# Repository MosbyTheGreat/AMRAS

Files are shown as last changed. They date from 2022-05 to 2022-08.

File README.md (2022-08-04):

# AMRAS
Anti-Mitbewohner-Raketen-Abwehr-System (engl. Anti Roommate Rocket Defence System)

An automated turret, which uses a combination of a Raspberry Pi, a camera, some servos, transformers and rubbing alcohol
to propel rubber rockets into anyone's face who dares to enter its vicinity.

The build manual can be found [here](./Manual/AMRAS%20Build%20Manual.pdf).

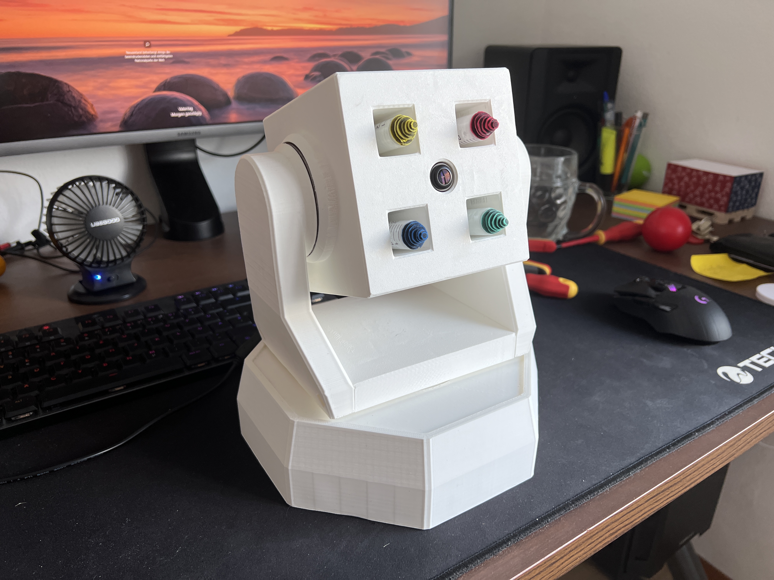
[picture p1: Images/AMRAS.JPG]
AMRAS


## Parts List

 - Raspberry Pi 3B (Good Luck finding one, but should also work with newer versions)  
 - Power Supply: https://www.amazon.de/gp/product/B07DG16TKS/ref=ppx_yo_dt_b_search_asin_title?ie=UTF8&psc=1  
 - Camera: https://de.aliexpress.com/item/32668508991.html  
 - Servo Controller: https://de.aliexpress.com/item/4000468996665.html  
 - 4x Transformer/Spark Generator: https://de.aliexpress.com/item/32872820437.html  
 - 2x Servo: https://de.aliexpress.com/item/32970493831.html  
 - 4-Band Relay: https://de.aliexpress.com/item/4001363470793.html  
 - Some Cables: https://de.aliexpress.com/item/33060775595.html  
 - 3x Ball Bearing: https://www.amazon.de/gp/product/B076ZL83YN/ref=ppx_yo_dt_b_asin_title_o03_s00?ie=UTF8&psc=1  
 - 4x Mini Magnets for keeping the Lid shut: https://www.magnet-shop.net/neodym/quadermagnete/quadermagnet-10.0-x-5.0-x-3.0-mm-n40-nickel-haelt-1.4-kg  
 - Syringes to craft Rockets out of: https://www.amazon.de/gp/product/B07MC7L4PG/ref=ppx_yo_dt_b_search_asin_image?ie=UTF8&psc=1  
 - Bunch of Screws (I used Wood screws to screw into the PLA):  
Raspi: 4x 2,0x10mm  
Kamera: 4x 2,0x10mm  
Main Body Fillings: 24x 2,9x13mm  
Arms: 4x 2,9x13mm  
Servo Shield: 4x 2,0x10mm  
Relais: 1x 2,0x10mm  

## Feature Ideas

 - Stereo camera to calculate distances and trajectory of projectiles
 - Different kinds of projectiles
 - Better servos to allow for 360° coverage
 - Live video feed to smartphone with manual control

## TODO
 - PID tuning
 - Script for camera calibration

## Credits

Initially inspired by this video:  
https://youtu.be/U4ndTDGhc1U

Credit to Adrian Rosebrock, PhD, from pyimagesearch.com for this wonderful tutorial, which my face tracking code is based on:  
https://www.pyimagesearch.com/2019/04/01/pan-tilt-face-tracking-with-a-raspberry-pi-and-opencv/

Also thanks to my roommate [Florian Geißegger BSc](mailto:florian.geissegger@gmx.com) for helping me with the soldering and for some general technical input.

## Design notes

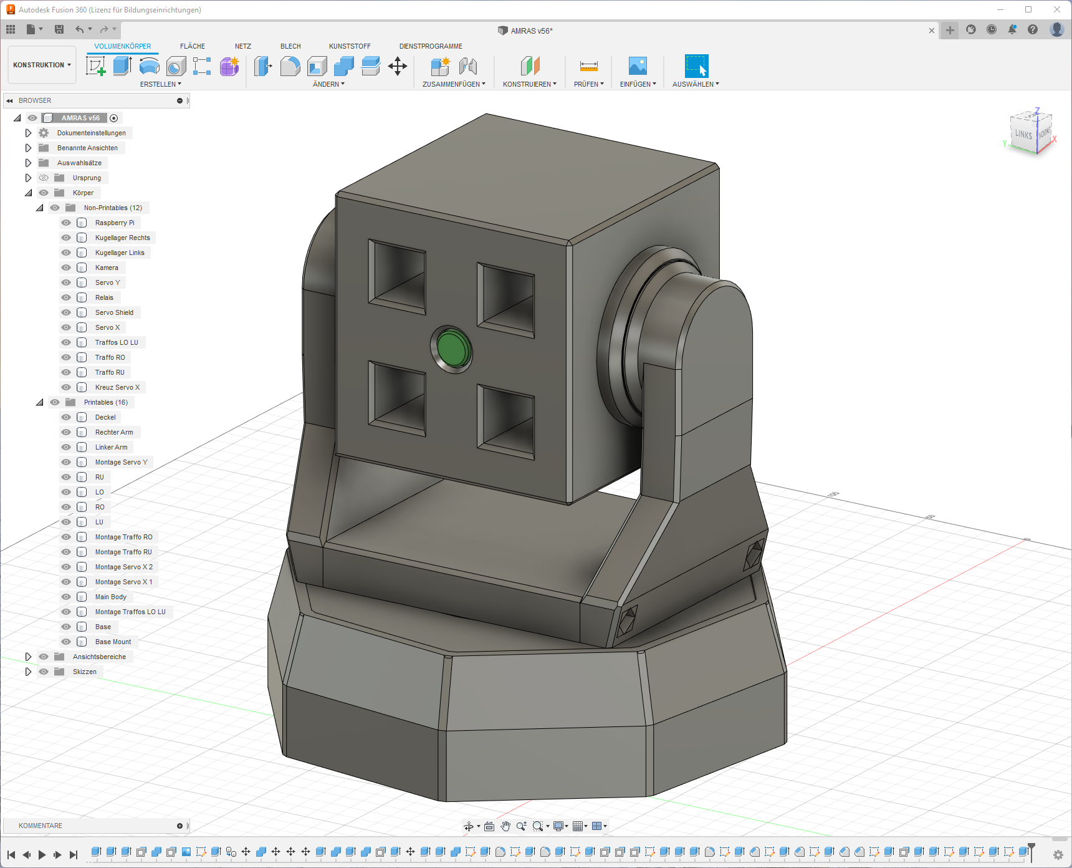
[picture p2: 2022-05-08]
Images/Fusion.png

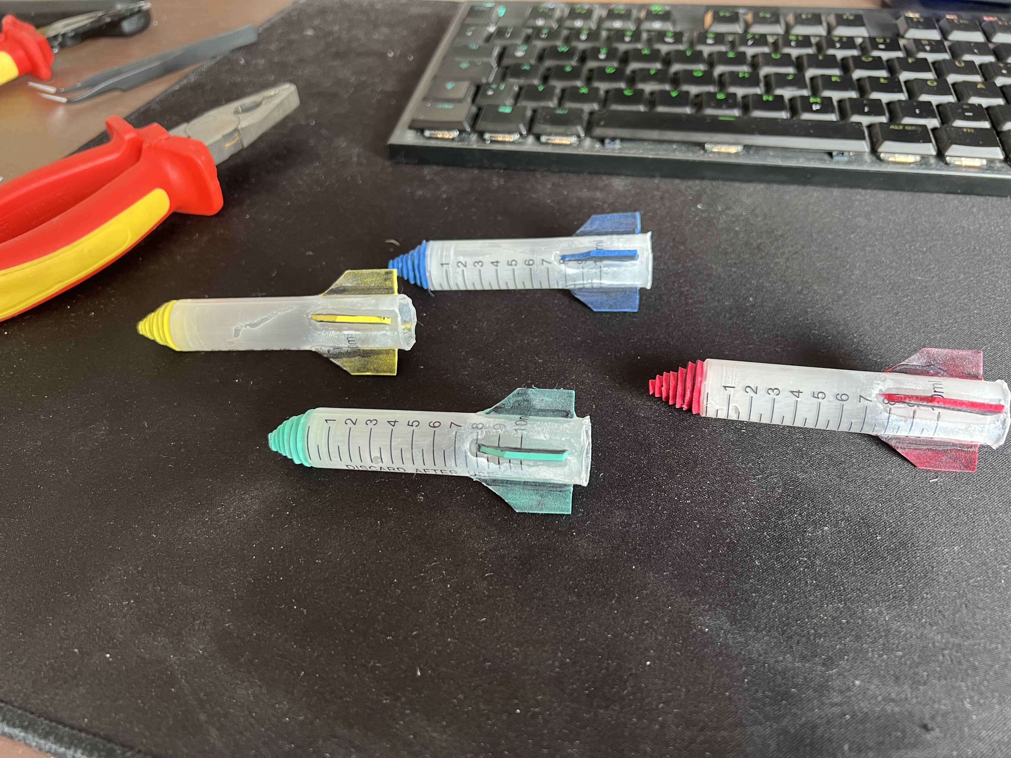
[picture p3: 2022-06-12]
Images/Rockets.JPG

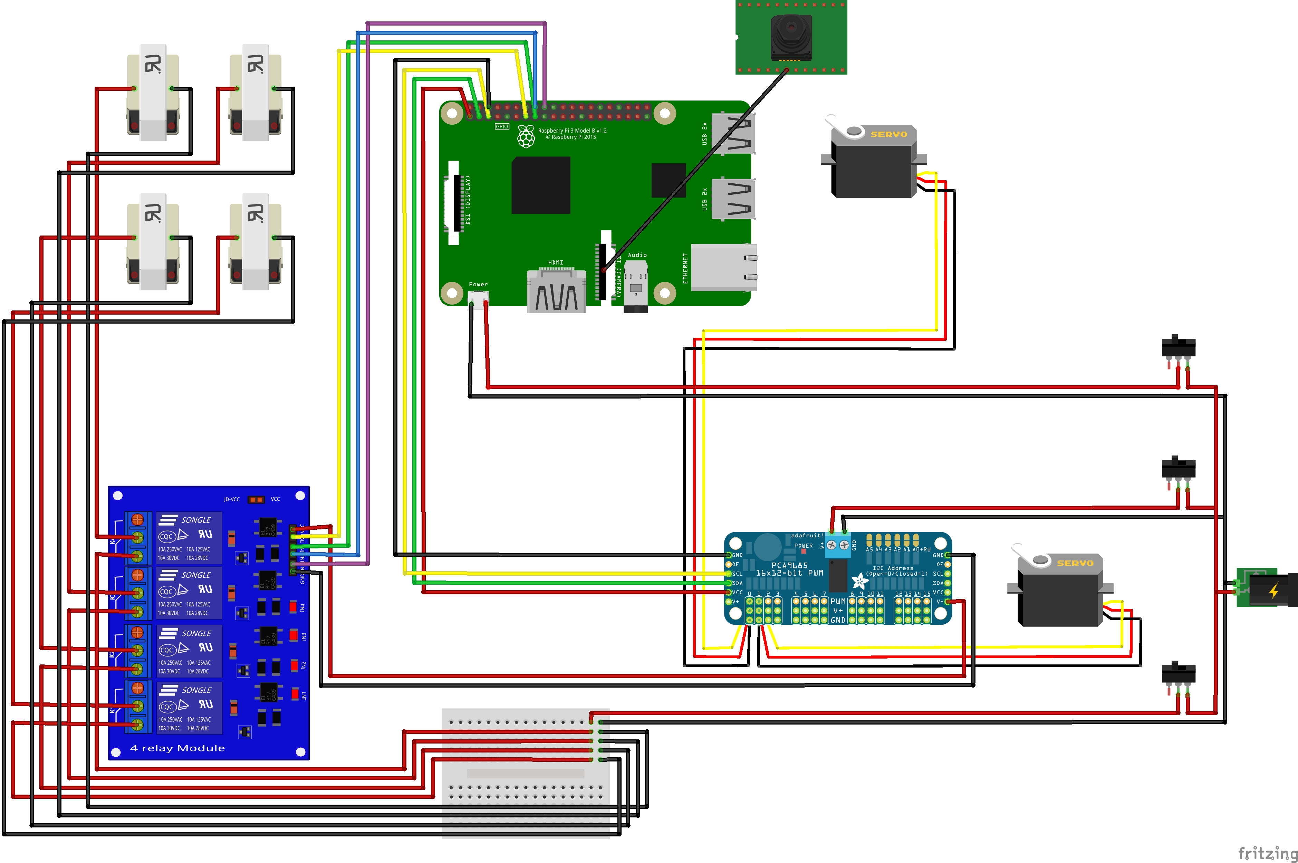
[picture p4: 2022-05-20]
Circuit Diagram/circuit_diagram.jpg

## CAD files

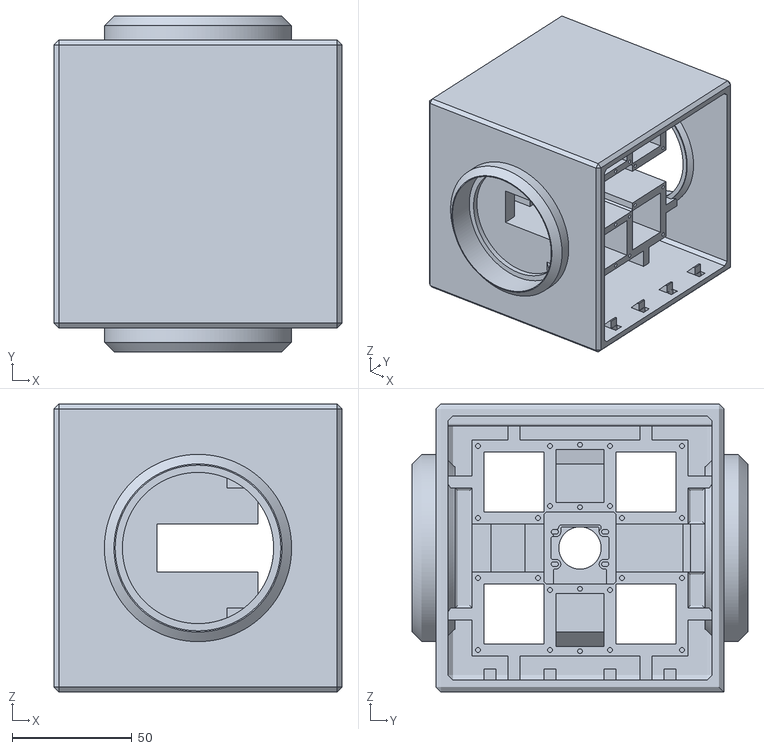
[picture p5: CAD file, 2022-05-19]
3D Files/Main Body.stl
120.0 x 140.0 x 120.0

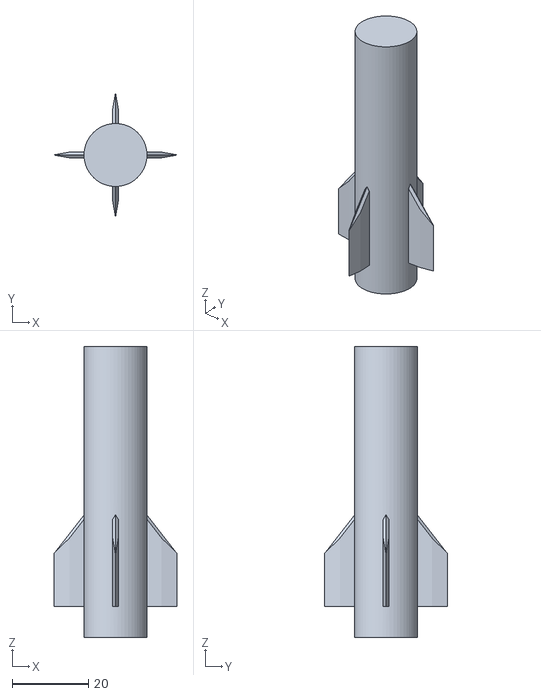
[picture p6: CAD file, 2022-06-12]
3D Files/Missile Fuelcell Flat Tip.stl
32.1 x 32.1 x 76.2

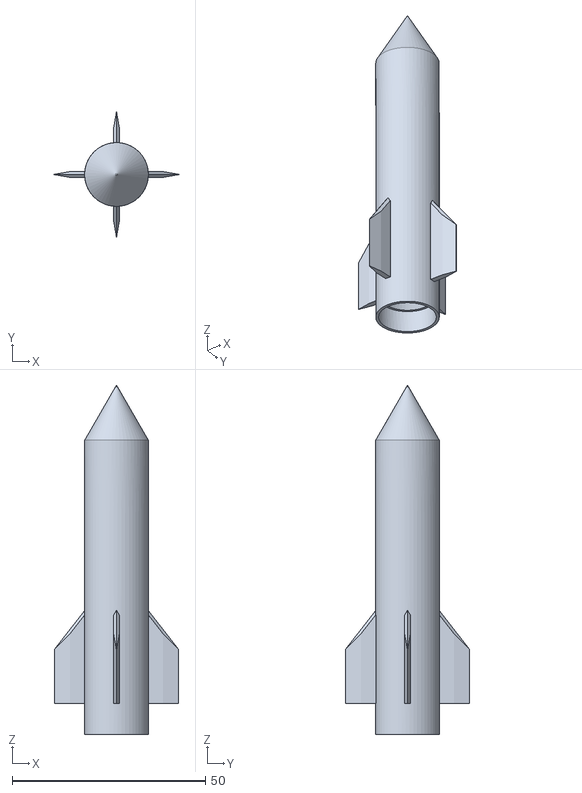
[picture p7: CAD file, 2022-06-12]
3D Files/Missile Fuelcell Spikyboi.stl
32.1 x 32.1 x 90.3

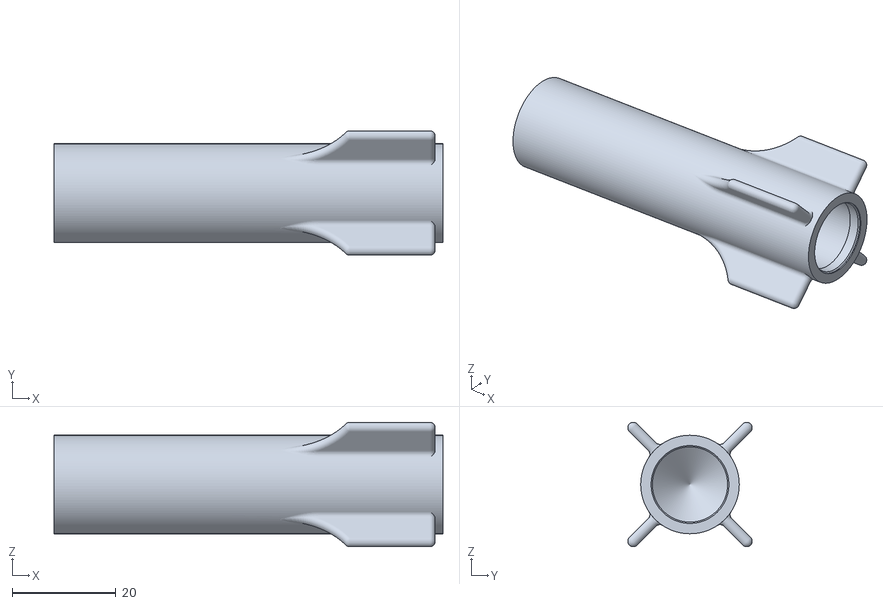
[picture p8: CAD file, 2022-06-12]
3D Files/Missile.stl
75.0 x 24.0 x 24.0

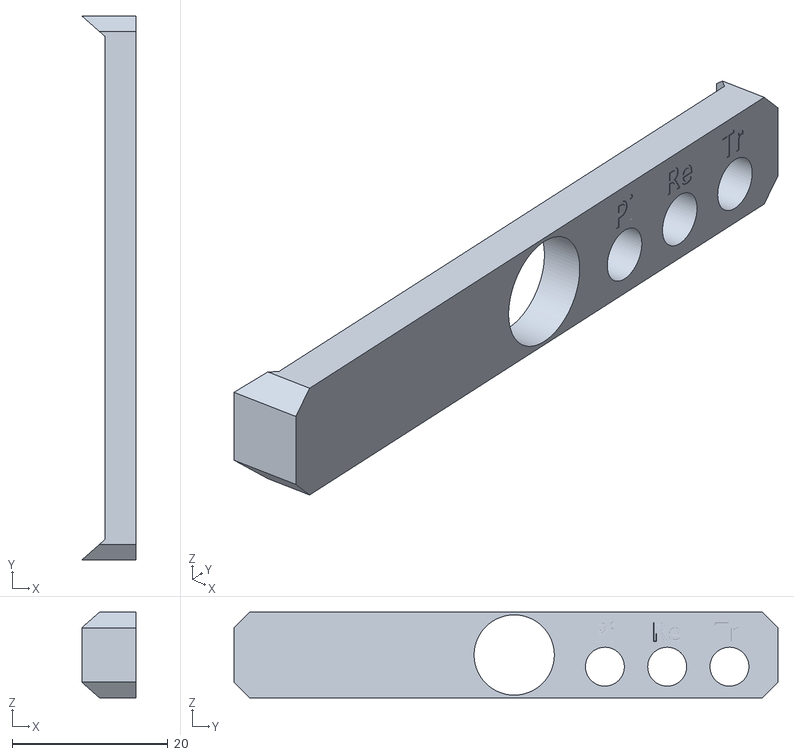
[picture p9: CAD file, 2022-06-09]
3D Files/Power Panel.stl
7.00 x 69.9 x 11.0

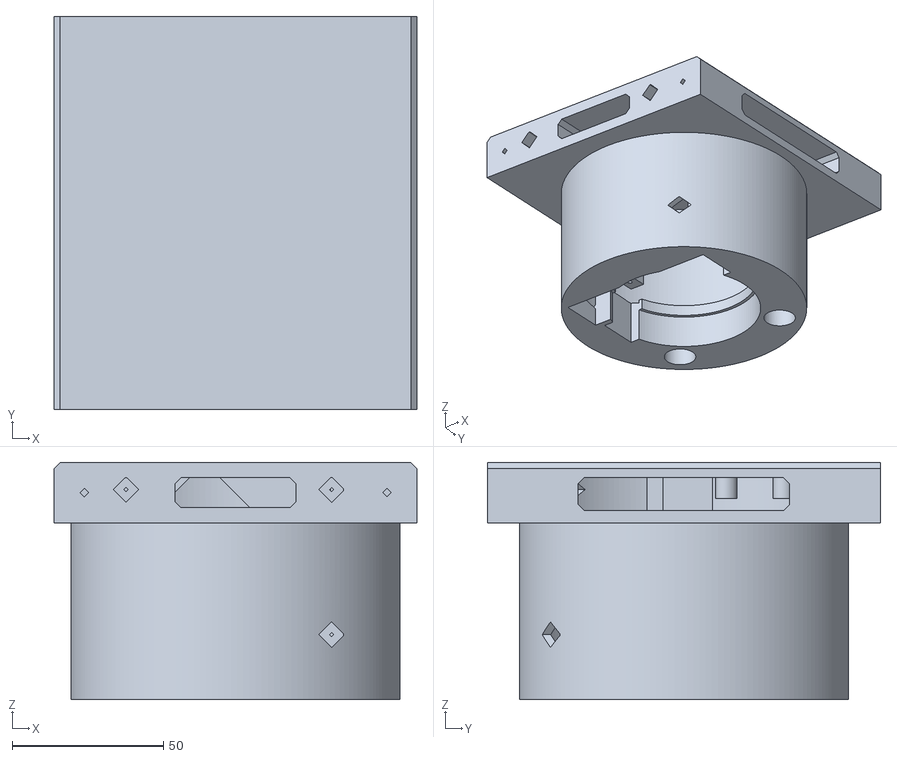
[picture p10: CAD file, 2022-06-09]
3D Files/Base Mount.stl
120.0 x 130.0 x 78.5

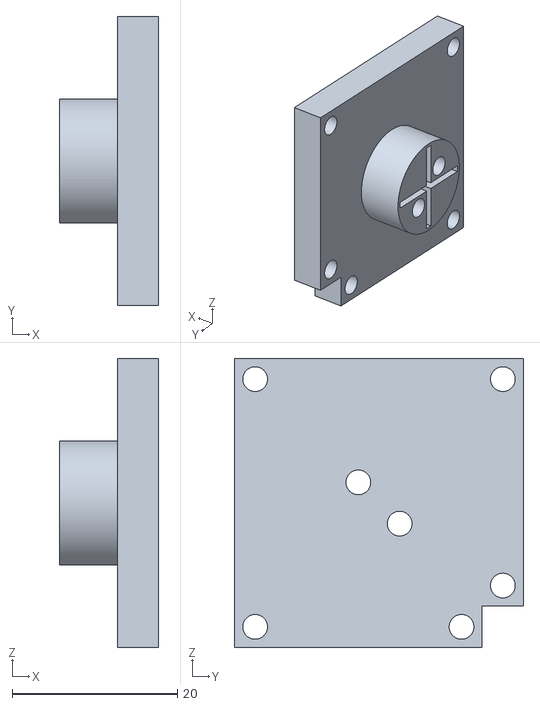
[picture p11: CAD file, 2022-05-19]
3D Files/LO.stl
12.0 x 35.0 x 35.0

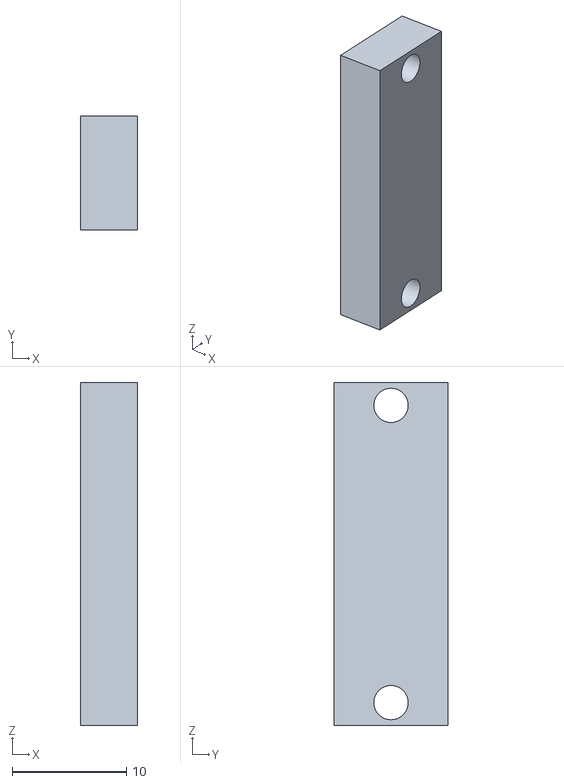
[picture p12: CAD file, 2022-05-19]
3D Files/Mount Traffo RU.stl
5.00 x 10.0 x 30.0

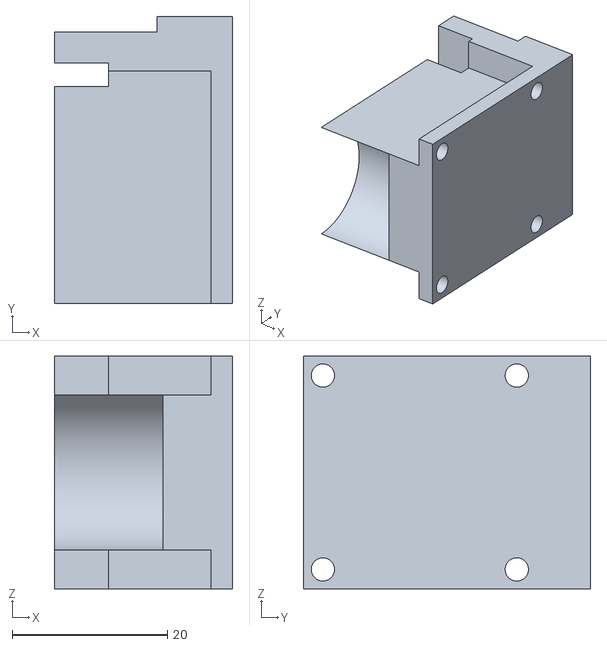
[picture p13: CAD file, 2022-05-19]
3D Files/Mount Servo Y.stl
23.0 x 37.0 x 30.0

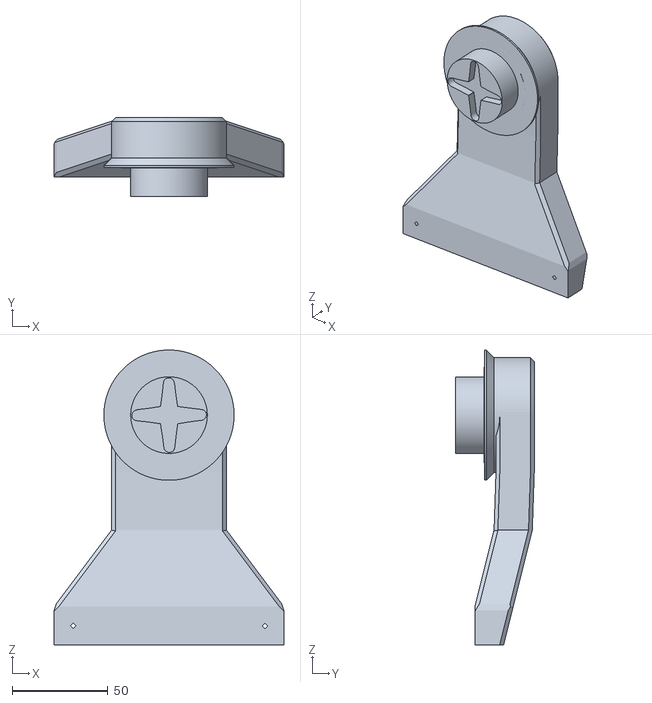
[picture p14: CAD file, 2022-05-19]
3D Files/Right Arm.stl
120.0 x 41.0 x 154.0

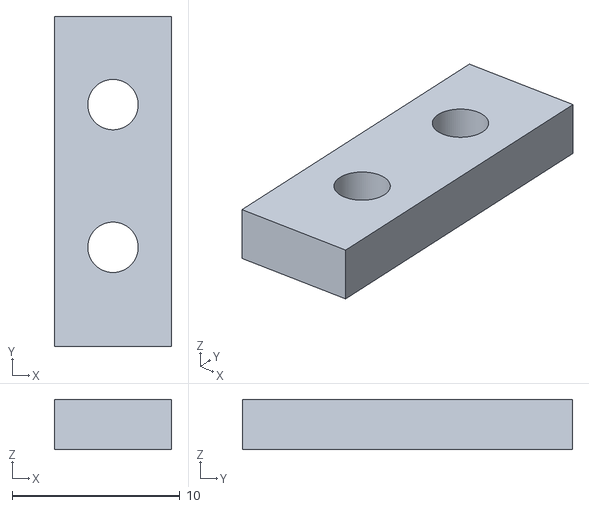
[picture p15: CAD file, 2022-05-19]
3D Files/Mount Servo X 2.stl
7.00 x 19.7 x 3.00

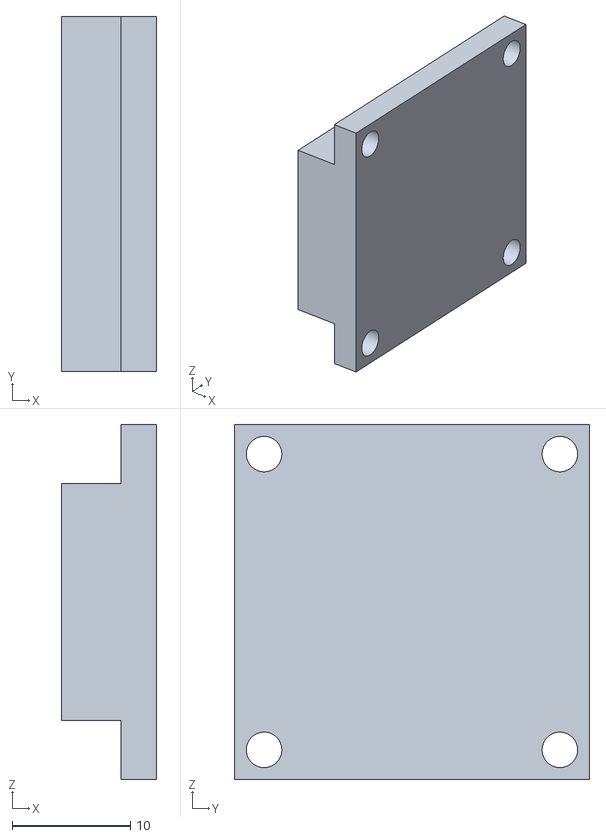
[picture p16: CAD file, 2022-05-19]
3D Files/Mount Traffos LO LU.stl
8.00 x 30.0 x 30.0

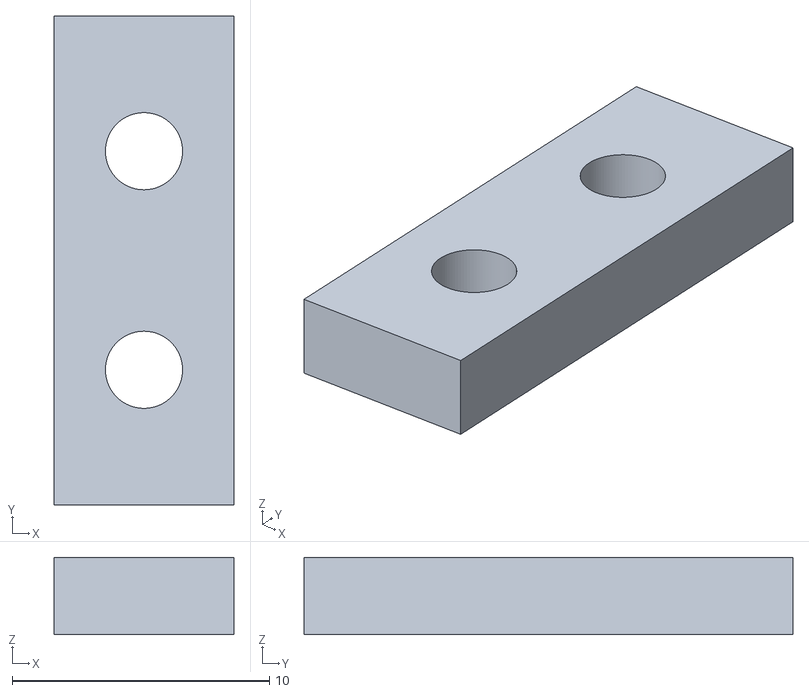
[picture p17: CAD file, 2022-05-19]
3D Files/Mount Servo X 1.stl
7.00 x 19.0 x 3.00

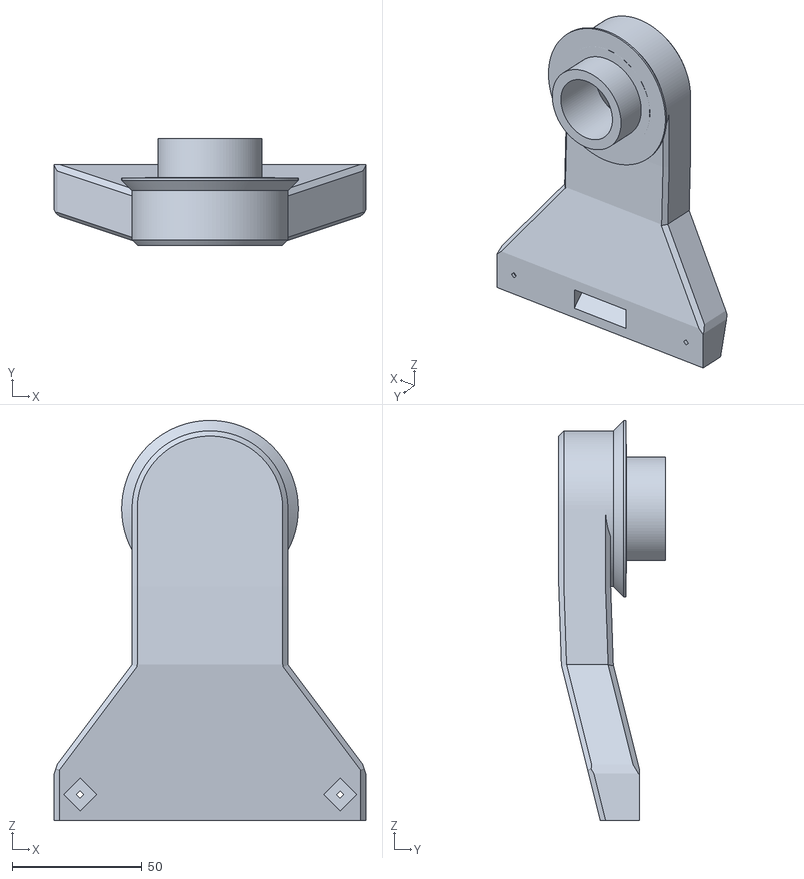
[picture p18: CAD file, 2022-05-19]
3D Files/Left Arm.stl
120.0 x 41.0 x 154.0

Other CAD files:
3D Files/RO.stl
3D Files/Mount Traffo RO.stl
3D Files/RU.stl
3D Files/Base.stl
3D Files/LU.stl
3D Files/Lid.stl

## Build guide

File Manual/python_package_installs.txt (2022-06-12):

Package installs:
sudo pip3 install opencv-python
sudo pip3 install smbus
sudo pip3 install imutils
sudo pip3 install "camera[array]"
sudo pip3 install adafruit_servokit
sudo pip3 install adafruit_motor
sudo pip3 install numpy
sudo pip3 install matplotlib

use 'sudo raspi-config' to go to raspberry pi configurantion and enable i2c & camera

Command for Starting program:
python3 init_amras.py -c frontalface.xml

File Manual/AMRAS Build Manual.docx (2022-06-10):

# AMRAS Build Manual

Screencap from the 3D Model in Fusion

# Introduction

AMRAS is the abbreviation for the German long form “Anti-Mitbewohner-Raketen-Abwehr-System” which translates to Anti-Roommate-Rocket-Defence-System.

It uses a combination of a Raspberry Pi, a camera, some servos, trafos and methylated spirits to propel rubber rockets into anyone’s face who dares to enter its vicinity

This guide will show you how to build and start it, have fun!

I got inspired when reddit flushed this video (https://youtu.be/U4ndTDGhc1U) onto my frontpage and I thought “that’s kinda cool, but I have a 3D printer and a Raspberry Pi, I could do that better”.

My code is based on Adrian Rosebrock’s tutorial (https://www.pyimagesearch.com/2019/04/01/pan-tilt-face-tracking-with-a-raspberry-pi-and-opencv/) who used a similar setup to track faces. While he used a PID controller for moving the servos, I had to fall back to a simpler movement, but this will hopefully soon be fixed.

# Parts List

These are not affiliate links, just the parts I used. It should also work with slightly different hardware, but then you would need to adapt the 3D models for mounting holes

- A Raspberry Pi 3B (a newer version should also work, but this is what I have tested with
- A 5V Power supply and some way of distributing power
- Camera (https://de.aliexpress.com/item/32668508991.html)
- Servo Controller (https://de.aliexpress.com/item/4000468996665.html)
- 4x Transformer/Spark generator (https://de.aliexpress.com/item/32872820437.html)
- 2x Servo (https://de.aliexpress.com/item/32970493831.html)
- 4-Band Relais (https://de.aliexpress.com/item/4001363470793.html)
- Some Cables (https://de.aliexpress.com/item/33060775595.html)
- 3x Ball Bearing (https://www.amazon.de/gp/product/B076ZL83YN/ref=ppx_yo_dt_b_asin_title_o03_s00?ie=UTF8&psc=1)
- 4x Mini Magnets (https://www.magnet-shop.net/neodym/quadermagnete/quadermagnet-10.0-x-5.0-x-3.0-mm-n40-nickel-haelt-1.4-kg) for keeping the lid shut
- Syringes (https://www.amazon.de/gp/product/B07MC7L4PG/ref=ppx_yo_dt_b_search_asin_image?ie=UTF8&psc=1) to craft rockets out of
- 3x Switches (https://www.amazon.de/gp/product/B07CG7JYF8/ref=ppx_yo_dt_b_asin_title_o00_s00?ie=UTF8&psc=1)
- Micro USB Cable to provide power for the Raspberry Pi (or USB-C if using a newer model)
- SD Card with minimum 8GB for the operating system
- Bunch of Screws (I used Wood Screws) Raspi: 4x 2,0x10mm

Kamera: 4x 2,0x10mm

Main Body Fillings: 24x 2,9x13mm

Arms: 4x 2,9x13mm

Servo Shield: 4x 2,0x10mm

Relais: 1x 2,0x10mm

- All printed 3D parts

# Assembly

## Software 1

### Installing Raspberry Pi OS

Install Raspberry Pi OS on the SD card and boot your Raspberry Pi.

### Installing the necessary python packages

Open the terminal on your raspberry pi and enter following commands:

sudo pip3 install opencv-python

sudo pip3 install smbus

sudo pip3 install imutils

sudo pip3 install "camera[array]"

sudo pip3 install adafruit_servokit

sudo pip3 install adafruit_motor

### Configuring the Raspberry Pi

Enter ‘sudo raspi-config’ to open the Raspberry Pi Software Configuration Tool, go to ‘Advanced’ and enable Camera and I2C (and SSH, if you want to control AMRAS remotely)

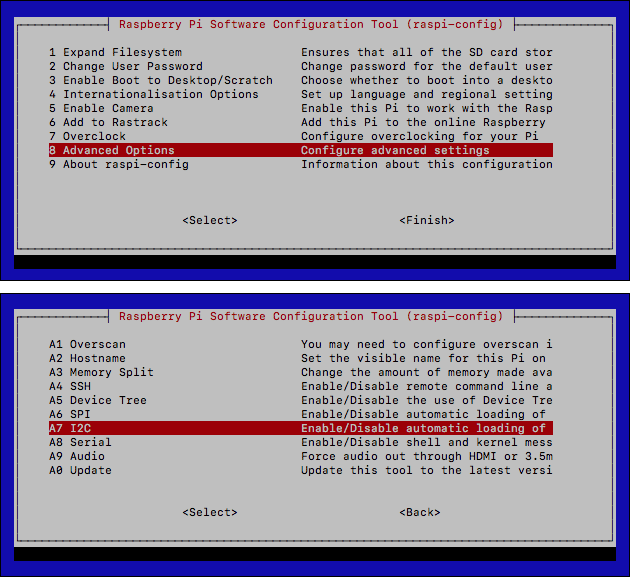
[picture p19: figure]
IC2 Sensor am Raspberry Pi nutzen (z.B. BH1750)

Figure 1 Raspberry Pi Software Configuration Tool

## Hardware

### Dry Running

I recommend connecting all parts according to the circuit diagram first, just so you don’t end up having any missing/broken parts which will need to be swapped. (This can be quite tedious, trust me)

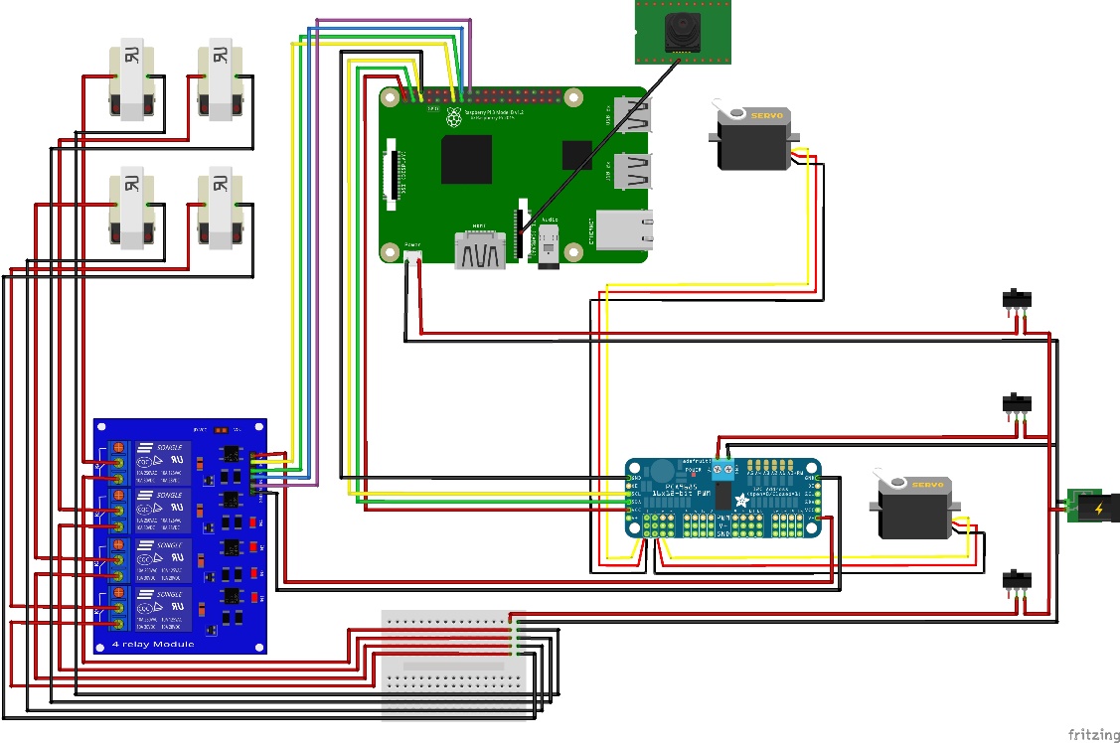
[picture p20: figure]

Figure 2 Circuit Diagram

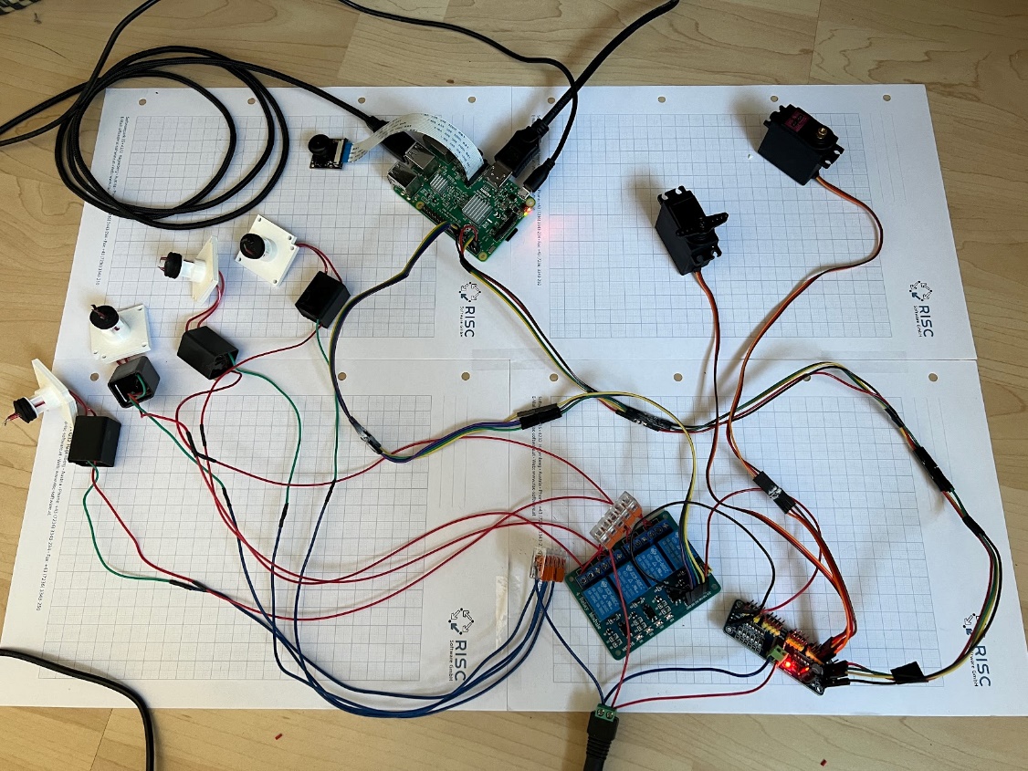
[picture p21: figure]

Figure 3 This is just ~90% correct, I forgot to take a new picture after making some adjustments

After making sure everything is connected properly, run test_servos.py to check functionality.

Try not to move the servos afterwards, as this would move the home/default position of AMRAS.

### Glueing Magnets

Start by glueing the magnets for the lid in place, making sure to have the proper polarity.

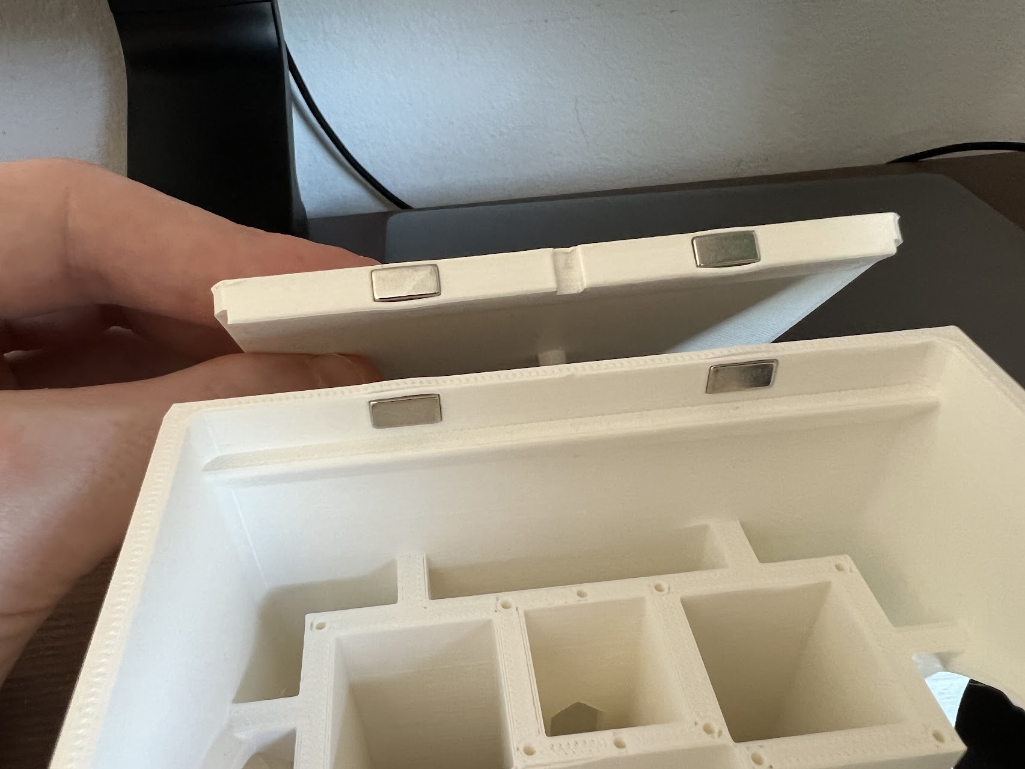
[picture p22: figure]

Figure 4 Lid and Main Body with the Magnets

### Installing the Camera

Screw in the Camera, the ribbon cable should fit into the recess below it.

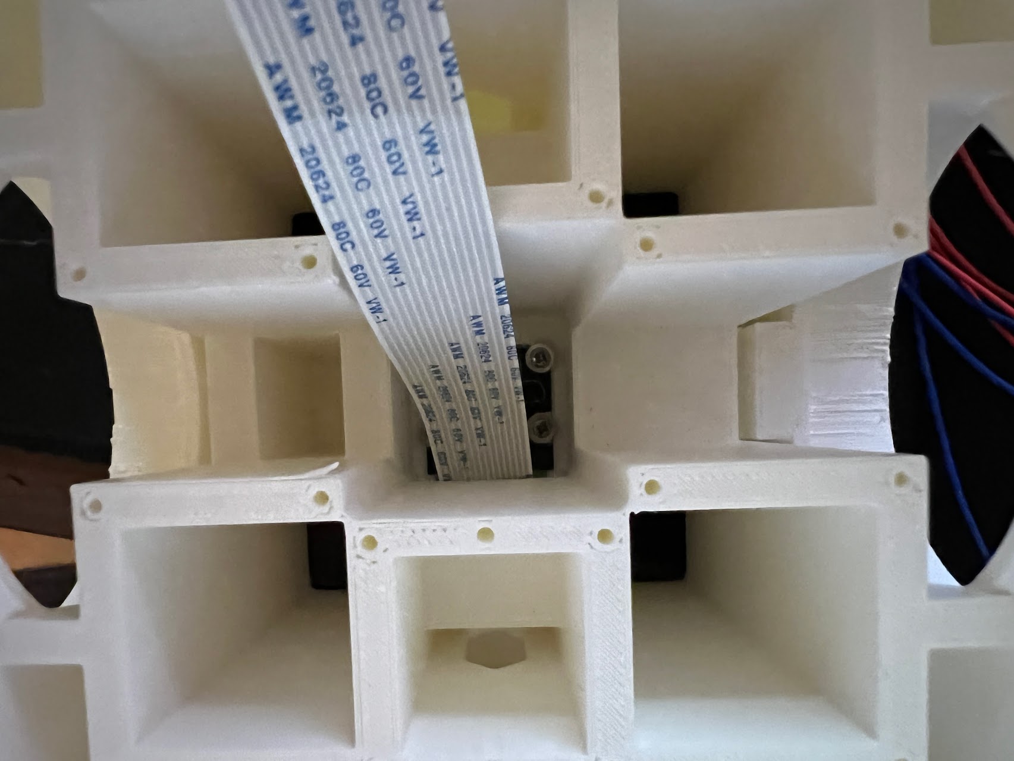
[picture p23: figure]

Figure 5 The Camera screwed in place

### Preparing and installing the trafos

Poke two holes through the end pieces of the syringes and passthrough the output cables of the trafos through both the mount and the syringe end piece. The endpiece needs to be cut off to be slotted into the cross-holes.

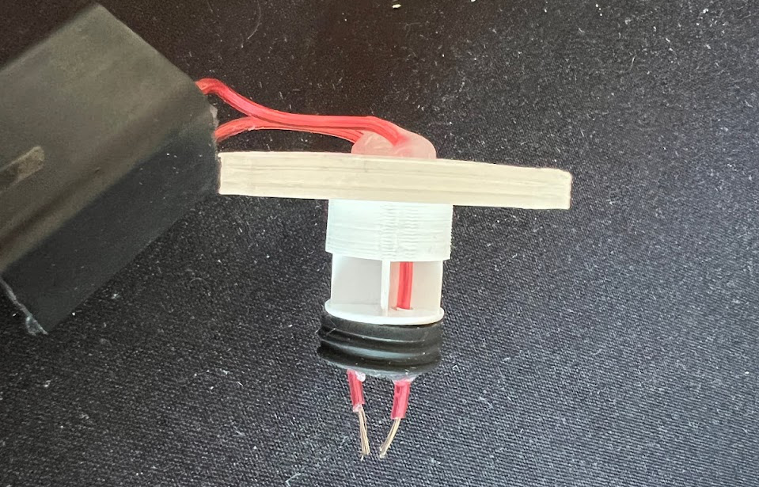
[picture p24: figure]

Figure 6 Installation of trafo, syringe endpiece and mount

After making sure you have enough cable length to mount the trafos in the main body, glue the cables in place.

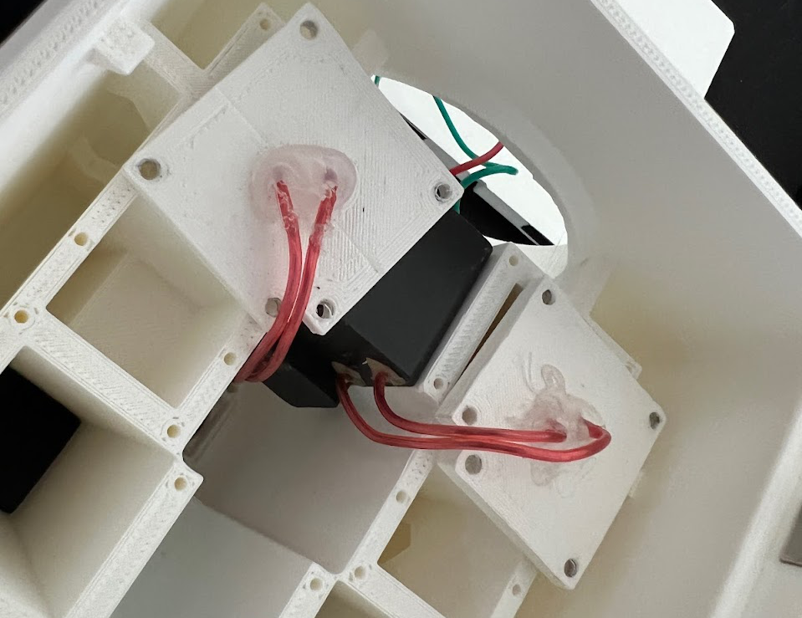
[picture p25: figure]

Figure 7 Checking the cable length

The input cables of the trafos will need to be extended for about 30cm, to be able to reach through the arms, I also recommend marking them by colour, to be able to differentiate them later.

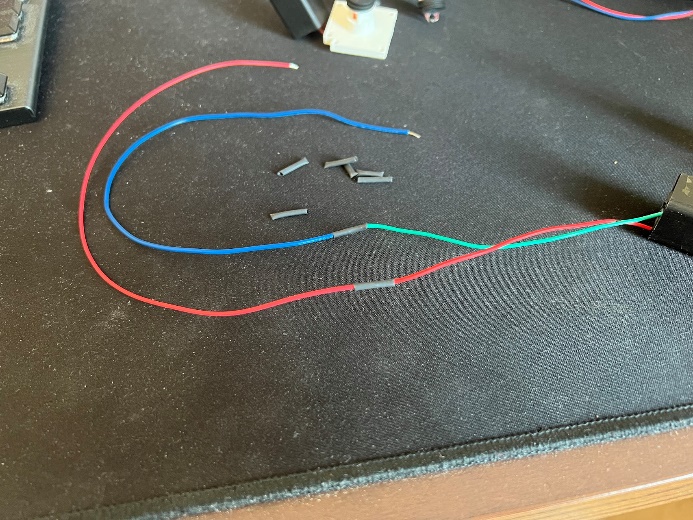
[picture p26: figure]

Figure 8 Cable extensions

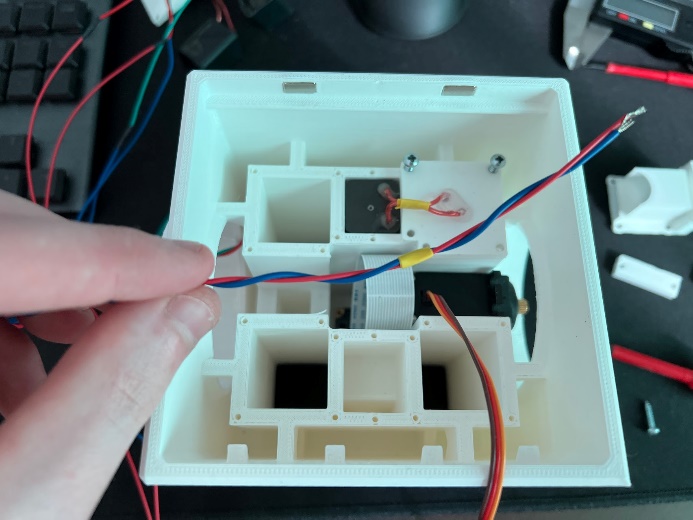
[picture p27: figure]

Figure 9 Colour-coding

Now it is time to mount all the trafos and servo Y, while also putting the cables in the right places.

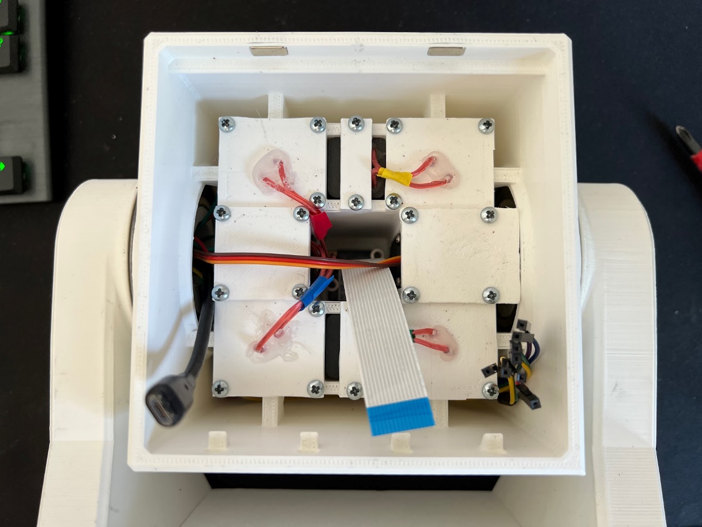
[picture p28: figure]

Power for Raspberry Pi

Cables to Raspberry Pi

RU

RO

LU

LO

Figure 10 Main Body all parts installed

### Mounting the Raspberry Pi

Screw the Raspberry Pi into the provided space on the lid, making sure to pay attention to the orientation.

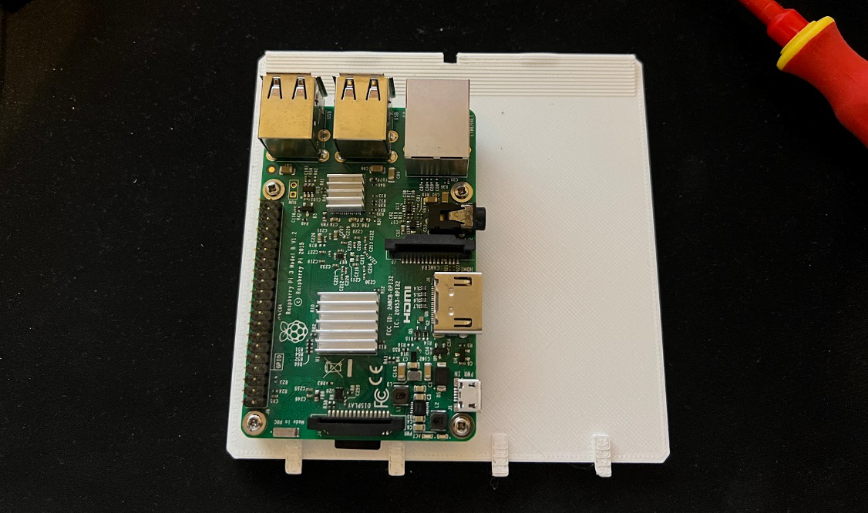
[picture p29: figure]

Figure 11 The mounted Raspberry Pi

Plug in the cables and close the lid for now.

### Adding the arms

Put the ball bearings into place and add the arms, while passing the cables through.

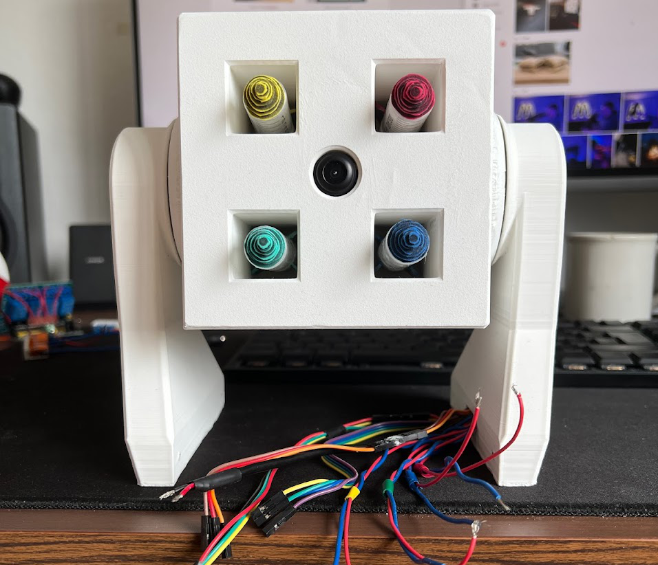
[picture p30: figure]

Figure 12 Arms and ball bearings added

### Wiring the Base Mount

## Software 2

### Running AMRAS

If everything is connected properly, it should now be as easy as running init_amras.py.

For calibrating I recommend plugging in the Raspberry Pi into a monitor with mouse and keyboard, afterwards it is easily possible to just run it using SSH.

You can alter the mid_offset (line 24 in init_amras.py) variable for calibration in case the camera is not mounted perfectly flush/centered.
Also, you might want to play around bit with the translation multiplier (line 22), but I decided it is good enough for me, also getting the PID controller to work is the goal anyways.

### Command Line Arguments

It is possible to provide some arguments when running the program, to change the console output, the movement implementation...

Arg | Type | Required | Default | Description
-c, --cascade | String | True | - | Path to the haar cascade
-a, --armed | Bool | False | False | Option to arm the turret
-p, --pid | Bool | False | False | Option to use PID over more basic movement
-v, --verbose | Bool | False | False | Option to show console output
-I, --image | Bool | False | False | Option to draw image

Examples:

python3 init_amras.py -c frontalface.xml -a True

Starts AMRAS without showing any output, tracking faces, and shooting when on target.

python3 init_amras.py -c ball.xml -i True -v True

Starts AMRAS while showing various values I the console, also enables camera feed and will track balls, recommended for calibrating the offset.

Moritz Larndorfer moritz.larndorfer@gmail.com

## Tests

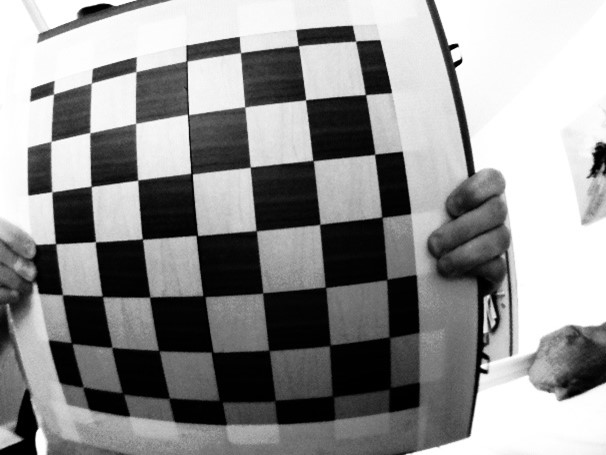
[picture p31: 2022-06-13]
Camera Calibration/Images/Bild1.jpg

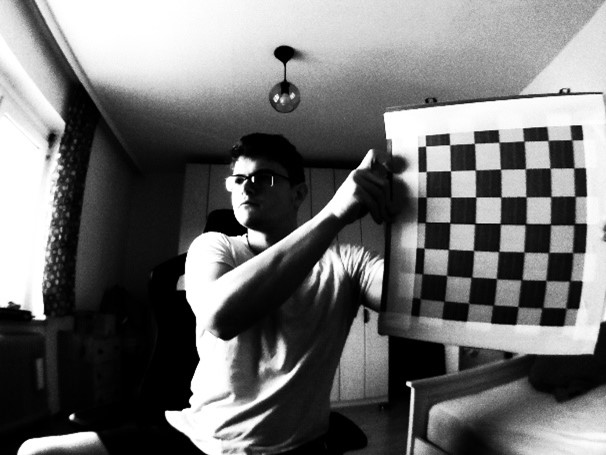
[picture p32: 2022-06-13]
Camera Calibration/Images/Bild2.jpg

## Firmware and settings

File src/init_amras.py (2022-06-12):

from math import ceil
from multiprocessing import Manager
from multiprocessing import Process
from imutils.video import VideoStream
from pyimagesearch.objcenter import ObjCenter
from pyimagesearch.pid import PID
from adafruit_servokit import ServoKit
import RPi.GPIO as GPIO
import numpy as np
import argparse
import signal
import time
import sys
import cv2

# init servos
kit = ServoKit(channels=16)
servo_pan = 1
servo_tilt = 0

multiplier = 0.1 # for translation from error to servo movement
servo_range = [1, 180]
mid_offset = [0, 0] # if the camera is not mounted perfectly flat/centered

#init GPIO Pins
GPIO.setmode(GPIO.BCM)

firing_pins = [22, 23, 24, 27]

for pin in firing_pins:
    GPIO.setup(pin, GPIO.OUT)
    GPIO.output(pin, GPIO.LOW)

# camera parameters to undistort images
camera_matrix = np.array([[1.52244073e+03,  0.00000000e+00, 1.18803566e+03],
                          [0.00000000e+00,  1.50426034e+03, 7.84669829e+02],
                          [0.00000000e+00,  0.00000000e+00, 1.00000000e+00]])
dist_coefs = np.array([-0.31086836,  0.10644732,  0.0030072,  -0.0012158,  -0.01891462])


# function to handle keyboard interrupt
def signal_handler(sig, frame):
    # print a status message
    print("You pressed `ctrl + c`! Exiting...")

    # reset servos to default position
    kit.servo[servo_pan].angle = 90
    kit.servo[servo_tilt].angle = 90

    # exit
    sys.exit()


def obj_center(args, obj_x, obj_y, center_x, center_y, search_flag, camera_matrix, dist_coefs):
    # signal trap to handle keyboard interrupt
    signal.signal(signal.SIGINT, signal_handler)

    # start the video stream and wait for the camera to warm up
    vs = VideoStream(usePiCamera=True).start()
    time.sleep(4.0)

    # initialize the object center finder
    obj = ObjCenter(args["cascade"])

    # loop indefinitely
    while True:
        # grab the frame from the threaded video stream
        frame = vs.read()

        # calculate the center of the frame as this is where we will
        # try to keep the object
        (H, W) = frame.shape[:2]
        center_x.value = W // 2
        center_y.value = H // 2

        if args["undistort"]:
            frame = cv2.undistort(frame, camera_matrix, dist_coefs, None, camera_matrix)

        # find the object's location
        object_loc = obj.update(frame, (center_x.value, center_y.value))
        ((obj_x.value, obj_y.value), rect) = object_loc


        # extract the bounding box and draw it
        if rect is not None:
            (x, y, w, h) = rect
            cv2.rectangle(frame, (x, y), (x + w, y + h), (0, 255, 0), 2)
            search_flag.value = 0
        else:
            search_flag.value = 1

        # display the frame to the screen
        if args["image"]:
            cv2.imshow("AMRAS Viewfinder", frame)
            cv2.waitKey(1)


def pid_process(output, p, i, d, obj_coord, center_coord):
    # signal trap to handle keyboard interrupt
    signal.signal(signal.SIGINT, signal_handler)

    # create a PID and initialize it
    p = PID(p.value, i.value, d.value)
    p.initialize()

    # loop indefinitely
    while True:
        # calculate the error
        error = center_coord.value - obj_coord.value

        # update the value
        output.value = p.update(error)


def in_range(val, start, end):
    # determine the input vale is in the supplied range
    return start <= val <= end


def set_servos_pid(pan, tilt):
    # signal trap to handle keyboard interrupt
    signal.signal(signal.SIGINT, signal_handler)

    # loop indefinitely
    while True:
        # the pan and tilt angles are reversed
        pan_angle = pan.value + 90
        tilt_angle = (tilt.value * -1) + 90
        print("Pan Angle:", pan_angle, "Tilt Angle:", tilt_angle)

        # if the pan angle is within the range, pan
        if in_range(pan_angle, servo_range[0], servo_range[1]):
            kit.servo[servo_pan].angle = pan_angle

        # if the tilt angle is within the range, tilt
        if in_range(tilt_angle, servo_range[0], servo_range[1]):
            kit.servo[servo_tilt].angle = tilt_angle

        time.sleep(0.1)


def set_servos(obj_x, obj_y, center_x, center_y, servo_position_x, servo_position_y, search_flag):
    # signal trap to handle keyboard interrupt
    signal.signal(signal.SIGINT, signal_handler)
    # give the camera time to warm up
    time.sleep(5.0)

    # shoot after x/10 seconds of being on target
    aim_timeout = 2
    aim_timeout_counter = aim_timeout

    firing_counter = 0

    # loop indefinitely
    while True:
        if search_flag.value == 0:
            error_x = obj_x.value - center_x.value + mid_offset[0]
            servo_position_x.value = smooth_move(error_x, servo_pan, servo_position_x.value)

            error_y = (obj_y.value - center_y.value + mid_offset[1]) * -1
            servo_position_y.value = smooth_move(error_y, servo_tilt, servo_position_y.value)

            if abs(error_x) < 10 and abs(error_y) < 10:
                if aim_timeout_counter == 0:
                    if (args["armed"]):
                        fire(firing_counter)
                        firing_counter = firing_counter + 1
                        time.sleep(2.0)
                    else:
                        print("Shoot!")
                    aim_timeout_counter = aim_timeout
                else:
                    if args["verbose"]:
                        print("Aim Timeout Counter:", aim_timeout)
                    aim_timeout_counter = aim_timeout_counter - 1
            else:
                if args["verbose"]:
                    print("Error x:", error_x, "Error y:", error_y)
                aim_timeout_counter = aim_timeout
        time.sleep(0.1)


def smooth_move(error, servo_nr, servo_position):
    new_pos = servo_position - ceil(error * multiplier)
    if in_range(new_pos, servo_range[0], servo_range[1]):
        kit.servo[servo_nr].angle = new_pos
        return new_pos
    else:
        return servo_position


def search_mode(servo_position_x, servo_position_y, search_flag):
    moving_direction = -1
    timeout = 50
    timeout_counter = timeout

    while True:
        if search_flag.value == 1:
            if timeout_counter == 0:
                kit.servo[servo_tilt].angle = 90
                servo_position_y.value = 90
                current_pos = servo_position_x.value

                if current_pos == 0 or current_pos == 180:
                    moving_direction = moving_direction * -1
                    kit.servo[servo_pan].angle = current_pos + moving_direction
                    servo_position_x.value = current_pos + moving_direction
                else:
                    kit.servo[servo_pan].angle = current_pos + moving_direction
                    servo_position_x.value = current_pos + moving_direction
            else:
                if args["verbose"]:
                    print("Timeout Counter:", timeout_counter)
                timeout_counter = timeout_counter -1
        else:
            timeout_counter = timeout
        time.sleep(0.1)


def fire(firing_counter):
    if firing_counter < 4:
        GPIO.output(firing_pins[firing_counter], GPIO.HIGH)
        time.sleep(0.5)
        GPIO.output(firing_pins[firing_counter], GPIO.LOW)
        if args["verbose"]:
            print("Projectile", firing_counter + 1, "fired!")
    else:
        if args["verbose"]:
            print("All projectiles fired!")


# check to see if this is the main body of execution
if __name__ == "__main__":
    # construct the argument parser and parse the arguments
    ap = argparse.ArgumentParser()
    ap.add_argument("-c", "--cascade", type=str, required=True, help="Path to input Haar cascade for detection")
    ap.add_argument("-a", "--armed", type=bool, required=False, default=False, help="Option to arm the turret")
    ap.add_argument("-p", "--pid", type=bool, required=False, default=False, help="Option to use PID or more basic movement") # PID not working at the moment
    ap.add_argument("-v", "--verbose", type=bool, required=False, default=False, help="Option to show console output")
    ap.add_argument("-i", "--image", type=bool, required=False, default=False, help="Option to draw image")
    ap.add_argument("-u", "--undistort", type=bool, required=False, default=False, help="Option to undistort images")
    args = vars(ap.parse_args())

    print("Welcome to AMRAS, your room will now be defended against nosy roommates.")

    if args["pid"]:
        print("PID movement will be used.")
    else:
        print("Basic pan/tilt movement will be used.")

    if args["armed"]:
        print("Weapon system is armed and ready.")
    else:
        print("Weapons are not armed, AMRAS will only work as a high-tech scarecrow.")
    
    if args["verbose"]:
        print("AMRAS will report everythign in the console.")
    if args["image"]:
        print("Video feed will be drawn.")
    if args["undistort"]:
        print("Images will be undistorted.")

    print("------------------------------------------------------------------------")

    # set servos to startung position
    kit.servo[servo_pan].angle = 90
    kit.servo[servo_tilt].angle = 90

    # start a manager for managing process-safe variables
    with Manager() as manager:
        # set integer values for the object center (x, y)-coordinates
        center_x = manager.Value("i", 0)
        center_y = manager.Value("i", 0)

        # set integer values for the object's (x, y)-coordinates
        obj_x = manager.Value("i", 0)
        obj_y = manager.Value("i", 0)

        # set integer values for servo positions
        servo_position_x = manager.Value("i", 90)
        servo_position_y = manager.Value("i", 90)

        # initialize search flag
        search_flag = manager.Value("i", 0)

        # we have 5 independent processes
        # 1. objectCenter  - finds/localizes the object
        # 2. panning       - PID control loop determines panning angle
        # 3. tilting       - PID control loop determines tilting angle
        # 4. setServosPID  - drives the servos to proper angles based
        #                    on PID feedback to keep object in center
        # 5. setServos     - drives the servos if not using PID, very basic

        process_object_center = Process(target=obj_center, args=(args, obj_x, obj_y, center_x, center_y, search_flag, camera_matrix, dist_coefs))
        process_search_mode = Process(target=search_mode, args=(servo_position_x, servo_position_y, search_flag))
        process_object_center.start()
        process_search_mode.start()

        if args["pid"]:
            # pan and tilt values will be managed by independed PIDs
            pan = manager.Value("i", 0)
            tilt = manager.Value("i", 0)

            # set PID values for panning
            pan_p = manager.Value("f", 0.0)
            pan_i = manager.Value("f", 0.0)
            pan_d = manager.Value("f", 0.0)

            # set PID values for tilting
            tilt_p = manager.Value("f", 0.0)
            tilt_i = manager.Value("f", 0.0)
            tilt_d = manager.Value("f", 0.0)

            process_panning = Process(target=pid_process, args=(pan, pan_p, pan_i, pan_d, obj_x, center_x))
            process_tilting = Process(target=pid_process, args=(tilt, tilt_p, tilt_i, tilt_d, obj_y, center_y))
            process_set_servos_pid = Process(target=set_servos_pid, args=(pan, tilt))

            process_panning.start()
            process_tilting.start()
            process_set_servos_pid.start()

            process_panning.join()
            process_tilting.join()
            process_set_servos_pid.join()
        else:
            process_set_servos = Process(target=set_servos, args=(obj_x, obj_y, center_x, center_y, servo_position_x, servo_position_y, search_flag))
            process_set_servos.start()
            process_set_servos.join()

        process_object_center.join()
        process_search_mode.join()

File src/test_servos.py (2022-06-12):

import time
from adafruit_servokit import ServoKit
import RPi.GPIO as GPIO

# Servos
kit = ServoKit(channels=16)

kit.servo[0].angle = 0
kit.servo[1].angle = 0
time.sleep(2.0)

kit.servo[0].angle = 90
kit.servo[1].angle = 90
time.sleep(2.0)

kit.servo[0].angle = 180
kit.servo[1].angle = 180
time.sleep(2.0)

kit.servo[0].angle = 90
kit.servo[1].angle = 90

# Relays
GPIO.setmode(GPIO.BCM)

Pin1 = 24
Pin2 = 23
Pin3 = 22
Pin4 = 27

GPIO.setup(Pin1, GPIO.OUT)
GPIO.setup(Pin2, GPIO.OUT)
GPIO.setup(Pin3, GPIO.OUT)
GPIO.setup(Pin4, GPIO.OUT)

GPIO.output(Pin1, GPIO.LOW)
GPIO.output(Pin2, GPIO.LOW)
GPIO.output(Pin3, GPIO.LOW)
GPIO.output(Pin4, GPIO.LOW)

GPIO.output(Pin1, GPIO.HIGH)
time.sleep(0.5)
GPIO.output(Pin1, GPIO.LOW)
time.sleep(2.0)

GPIO.output(Pin2, GPIO.HIGH)
time.sleep(0.5)
GPIO.output(Pin2, GPIO.LOW)
time.sleep(2.0)

GPIO.output(Pin3, GPIO.HIGH)
time.sleep(0.5)
GPIO.output(Pin3, GPIO.LOW)
time.sleep(2.0)

GPIO.output(Pin4, GPIO.HIGH)
time.sleep(0.5)
GPIO.output(Pin4, GPIO.LOW)
time.sleep(2.0)

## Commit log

2021-01-18 basic tracking and servos working
2021-01-22 Circuit Diagram + Fritzing File
    [RDT.fzz]
2021-11-09 STLs for 3D printing
2022-01-18 sonar properties
2022-01-18 Update pid.py to snake_case
2022-01-18 Show sonarcloud status
2022-05-05 Added init_haar and made folder from stl-zip
    [Base Mount.stl, Base.stl, Deckel.stl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]
2022-05-05 Some reqorganisation
    [AMRAS.fzz, Base Mount.stl, Base.stl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]
2022-05-05 Folder renamed
    [Base Mount.stl, Base.stl, Deckel.stl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]
2022-05-08 Base Mount updated, ball haar cascade
    [Base Mount.stl, Main Body.stl]
2022-05-11 Better fit for magnets
    [Deckel.stl, Main Body.stl]
2022-05-19 English names for STLs
    [Base Mount.stl, Base.stl, LO.stl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]
2022-05-19 PID stuff
2022-05-19 add set_servos withoud pid
2022-05-20 Update with info on screws
2022-05-20 Updated circuit diagram
    Added switches and rewired power to relais
    [AMRAS.fzz]
2022-05-31 begin calibrating pid controller
2022-05-31 tuple -> array for servo_positions
2022-06-09 manager for servo position values
2022-06-09 servo positions not getting updated
2022-06-09 Power Panel added
    [Base Mount.stl, Power Panel.stl]
2022-06-11 Manual finished, V1 done
    [AMRAS.fzz]
2022-06-11 Added glue to parts list
2022-06-12 3D missile files, manual updated
    [Missile.stl]
2022-06-12 More Missiles
    [Missile Fuelcell Flat Tip.stl, Missile Fuelcell Spikyboi.stl]
2022-06-12 Camera Calibration
2022-06-12 Renamed Folder
    [Base Mount.stl, Base.stl, LO.stl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]
2022-06-12 Camera Calibration finished
2022-06-12 increase timer to give camera more time to warm up
2022-06-12 camera matrix parameters corrected
    [init_amras.py]
2022-06-12 Camera Matrix
2022-06-13 chessboard for camera calibration added
